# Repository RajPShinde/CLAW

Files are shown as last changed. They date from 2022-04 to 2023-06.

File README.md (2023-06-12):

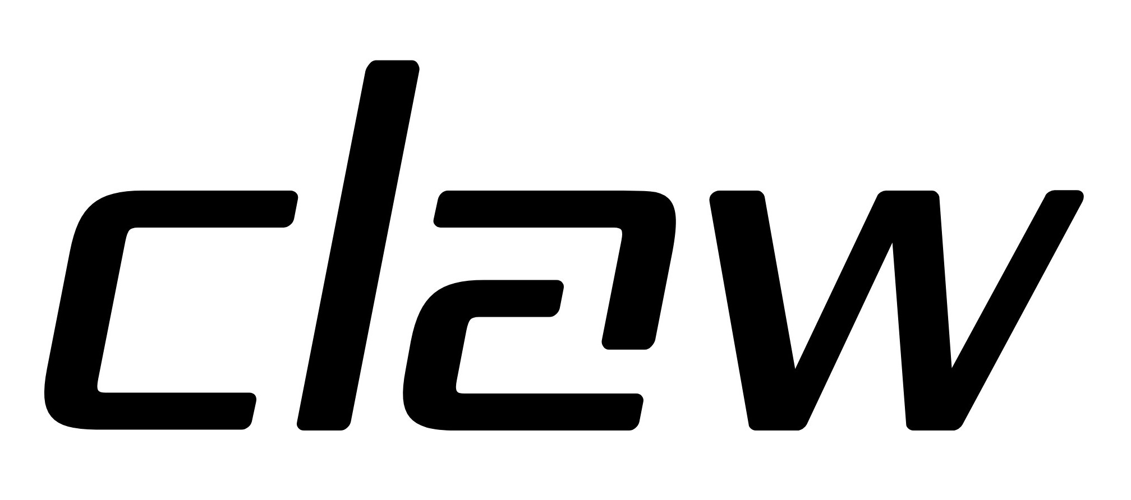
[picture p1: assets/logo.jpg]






---

## Overview
<p align="center">

</p>
An Open Source Quadruped Robot.
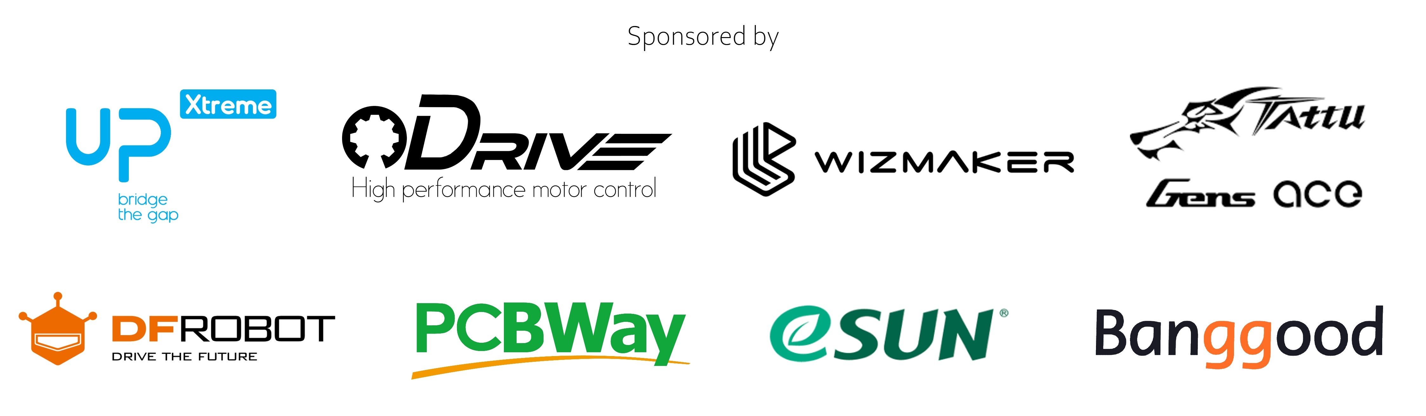
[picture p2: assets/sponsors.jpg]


## Dependencies
1. [ROS Noetic](http://wiki.ros.org/noetic)
2. [OCS2](https://github.com/leggedrobotics/ocs2)
3. [Eigen 3.4.0](https://eigen.tuxfamily.org/index.php?title=Main_Page)
4. [odrive_can](https://github.com/swankun/odrive_can)
5. [U8g2](https://github.com/olikraus/u8g2)

## Hardware
1. UP Xtreme i12- Core i5-1250PE 16GB RAM
2. Odrive 3.6 Motor Controller
3. Intel Realsense D435i
4. 8308 90Kv Outrunner BLDC
5. AS5047P Encoder
6. MCP2515 CAN Controller
7. MPU9265 9-DOF IMU
8. ADS1115 4-Channel ADC
9. WS2812B Addressable LED
10. SHI1106 128X64 OLED
11. MD30-60 Pressure Sensor

## Install & Build
```
mkdir -p ~/claw_ws/src
cd ~/claw_ws/src
git clone https://github.com/RajPShinde/CLAW
```

## TO-DO's
### CAD
- [x] Parts
- [x] Assembly
- [x] URDF
### Hardware Interface
- [x] PCB Design
- [x] SPI Test
- [x] I2C Test (MPU9255 & SH1106)
- [x] Socket CAN Test (MCP2515)
### Kinematics
- [x] Inverse Kinematics
- [x] Forward Kinematics
- [x] Velocity Kinematics
### Controls
- [ ] Hybrid Control (Impedance + Position)
### Trajectory Planning
- [x] Compound Cycloid
- [x] Bezier Curve
- [x] Jerk Minimized
### Visualization
- [x] Joint State Publishers
### Manager
- [ ] State Machine

## LICENSE
```
BSD 3-Clause License

Copyright (c) 2023, Raj Shinde
All rights reserved.

Redistribution and use in source and binary forms, with or without
modification, are permitted provided that the following conditions are met:

1. Redistributions of source code must retain the above copyright notice, this
   list of conditions and the following disclaimer.

2. Redistributions in binary form must reproduce the above copyright notice,
   this list of conditions and the following disclaimer in the documentation
   and/or other materials provided with the distribution.

3. Neither the name of the copyright holder nor the names of its
   contributors may be used to endorse or promote products derived from
   this software without specific prior written permission.

THIS SOFTWARE IS PROVIDED BY THE COPYRIGHT HOLDERS AND CONTRIBUTORS "AS IS"
AND ANY EXPRESS OR IMPLIED WARRANTIES, INCLUDING, BUT NOT LIMITED TO, THE
IMPLIED WARRANTIES OF MERCHANTABILITY AND FITNESS FOR A PARTICULAR PURPOSE ARE
DISCLAIMED. IN NO EVENT SHALL THE COPYRIGHT HOLDER OR CONTRIBUTORS BE LIABLE
FOR ANY DIRECT, INDIRECT, INCIDENTAL, SPECIAL, EXEMPLARY, OR CONSEQUENTIAL
DAMAGES (INCLUDING, BUT NOT LIMITED TO, PROCUREMENT OF SUBSTITUTE GOODS OR
SERVICES; LOSS OF USE, DATA, OR PROFITS; OR BUSINESS INTERRUPTION) HOWEVER
CAUSED AND ON ANY THEORY OF LIABILITY, WHETHER IN CONTRACT, STRICT LIABILITY,
OR TORT (INCLUDING NEGLIGENCE OR OTHERWISE) ARISING IN ANY WAY OUT OF THE USE
OF THIS SOFTWARE, EVEN IF ADVISED OF THE POSSIBILITY OF SUCH DAMAGE.
```

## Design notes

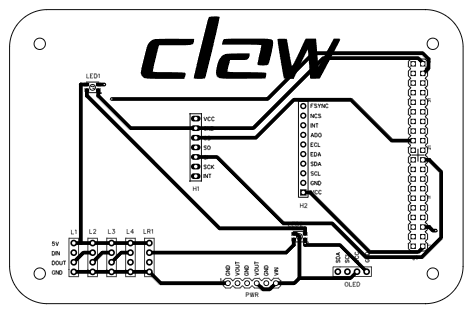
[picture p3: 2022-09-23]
PCB/PCB.png

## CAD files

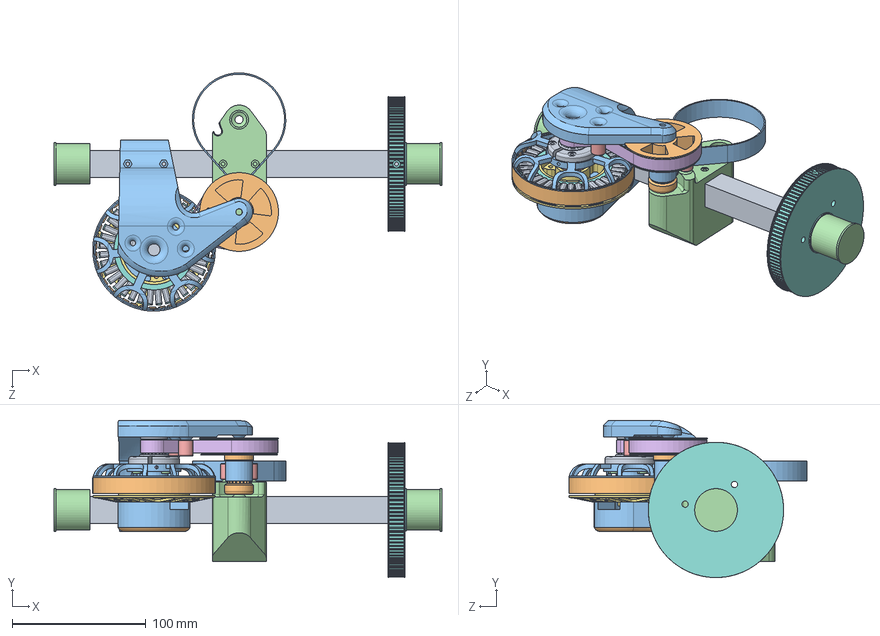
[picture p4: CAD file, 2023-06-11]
CAD/Assembly/Front Right Hip.SLDASM
290.3 x 117.6 x 178.3 mm
Hip Flexion & Abduction- HTD 3M 20T
Hip Flexion- HTD 3M 20T-60T
Hip Flexion- Motor Holder (Mirror)
Leg Holder (Mirror)
3xMR115 x 4
HTD 3M 10mm x 276mm
base.stp
stator.stp
coil.stp x 36
rotor.stp
outrunner.stp
screw-mount.stp x 4
6702ZZ-bearing-15x21x4.stp x 2
shaft.stp
fix-screw.stp
Hip Abduction- HTD 3M 105T (Mirror)
CF Hip
Hip Flexion Motor Holder Cover (Mirror)
HTD3M 15mm x 300mm
Shoulder Axle x 2

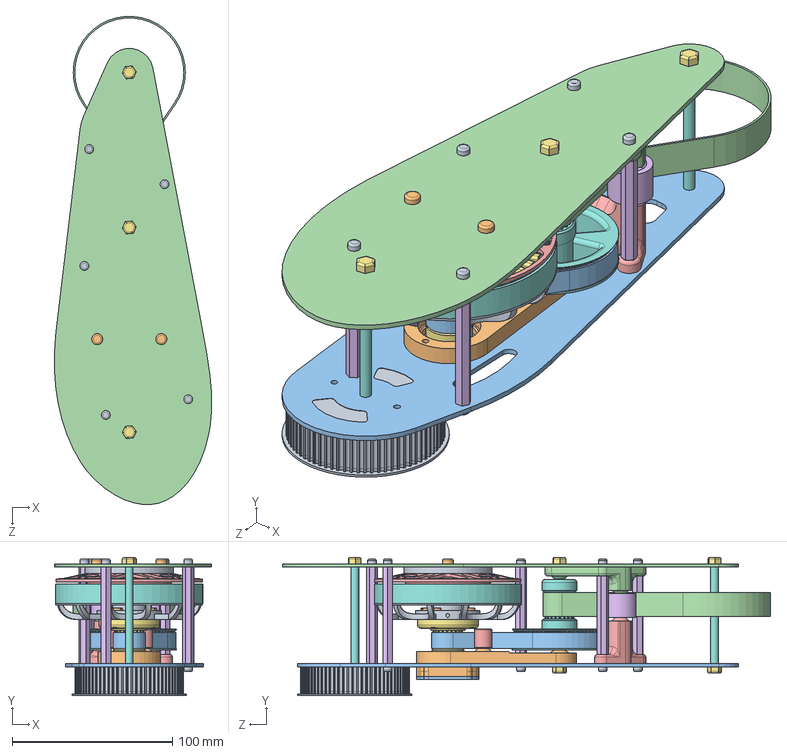
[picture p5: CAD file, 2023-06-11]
CAD/Assembly/Left Thigh.SLDASM
98.2 x 86.3 x 304.5 mm
Knee Motor Spacer
Knee Tensioner 1
Leg Plate- Inner
Leg Plate- Outer
base.stp
stator.stp
coil.stp x 36
rotor.stp
outrunner.stp
screw-mount.stp x 4
6702ZZ-bearing-15x21x4.stp x 2
shaft.stp
fix-screw.stp
Standoff 60mm x 5
Knee Flexion- HTD 3M 20T
Knee Flexion- HTD 3M 20T-60T
Hip Flexion- HTD 3M 72T
Knee Encoder Bottom Holder
Knee Encoder Top Holder
Knee Tensioner 2 Outer (Left Leg)
Knee Tensioner 2 Inner (Left Leg)
Knee Flexion- Idler x 2
M5 Nut x 5
M5 60mm x 2
M3 Screw 10mm x 10
M5 Screw 10mm x 2
HTD 3M 10mm x 276mm
HTD 3M 15mm x 348mm
3xMR115 x 2

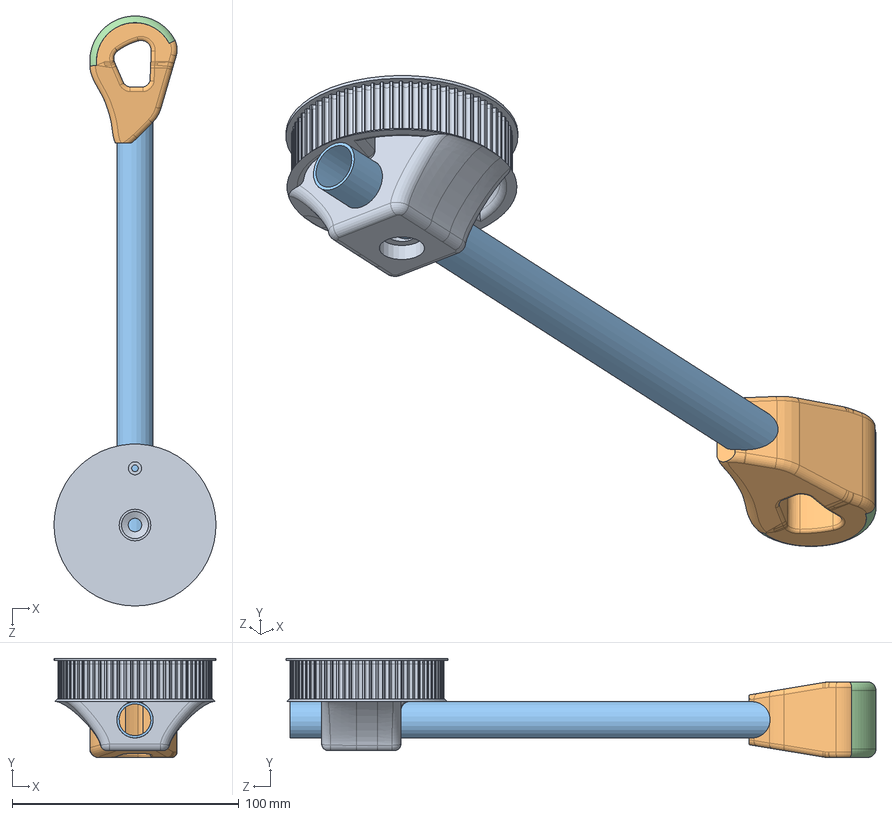
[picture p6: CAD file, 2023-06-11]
CAD/Assembly/Left Calf.SLDASM
71.4 x 43.8 x 260.2 mm
Knee Flexion- HTD 3M 72T
claw
CF Calf
Rubber Sole

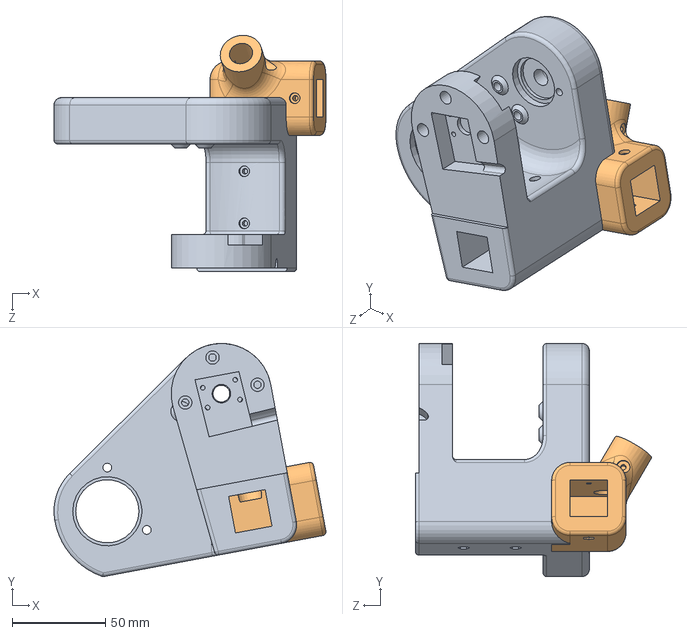
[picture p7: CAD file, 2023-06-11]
CAD/SPLDRT/Hip Abduction Motor Holder + Front Left Bracket.SLDASM
146.2 x 125.3 x 127.1 mm
Motor Holder- Hip Abduction
Front Left L Bracket

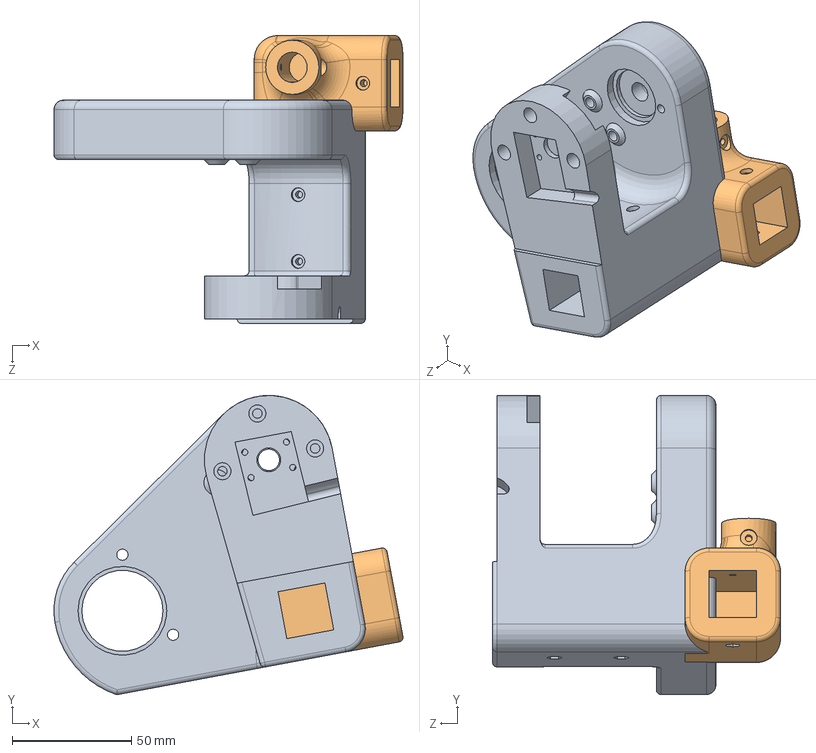
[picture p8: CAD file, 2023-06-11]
CAD/SPLDRT/Hip Abduction Motor Holder + Rear Right Bracket.SLDASM
146.2 x 125.3 x 120.7 mm
Motor Holder- Hip Abduction
Rear Right L Bracket

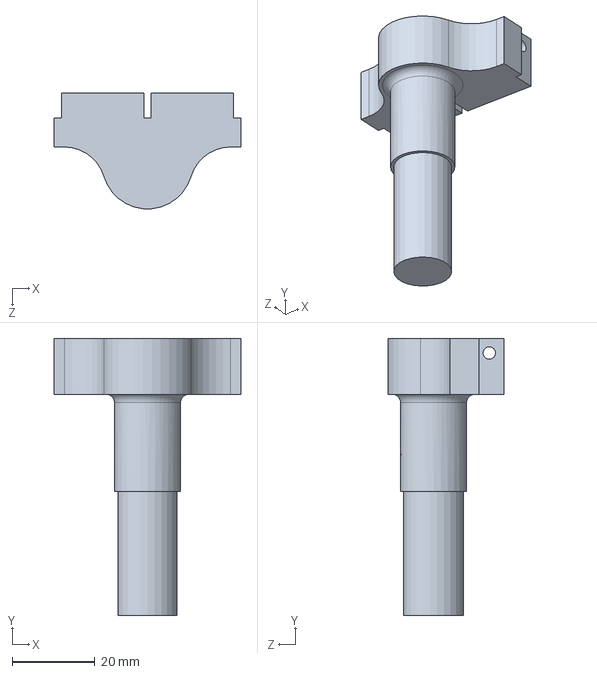
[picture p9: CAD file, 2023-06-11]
CAD/SPLDRT/Front Odrive Bracket.SLDPRT
45.1 x 67.0 x 27.9 mm

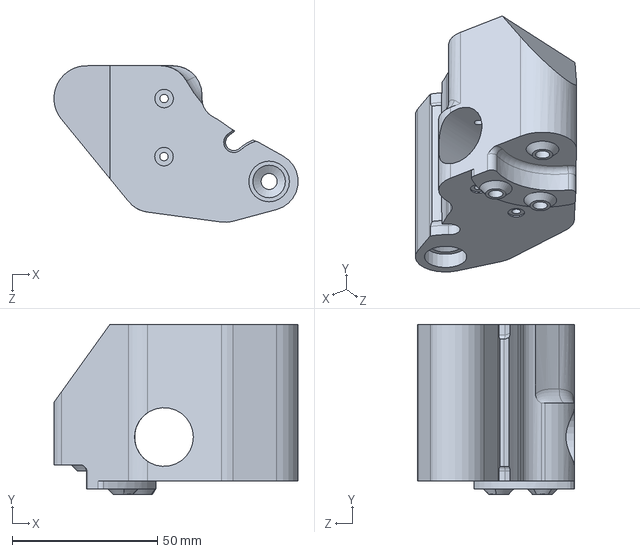
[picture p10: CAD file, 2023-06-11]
CAD/SPLDRT/Leg Hip Holder- Left.SLDPRT
84.0 x 58.6 x 53.9 mm

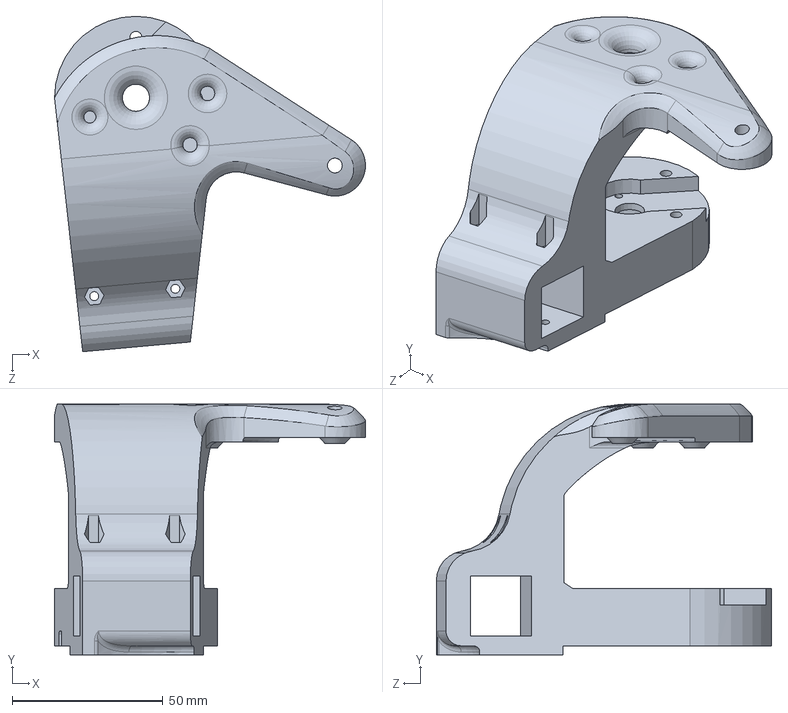
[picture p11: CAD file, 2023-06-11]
CAD/SPLDRT/Hip Flexion- Motor Holder.SLDPRT
103.1 x 83.1 x 111.2 mm

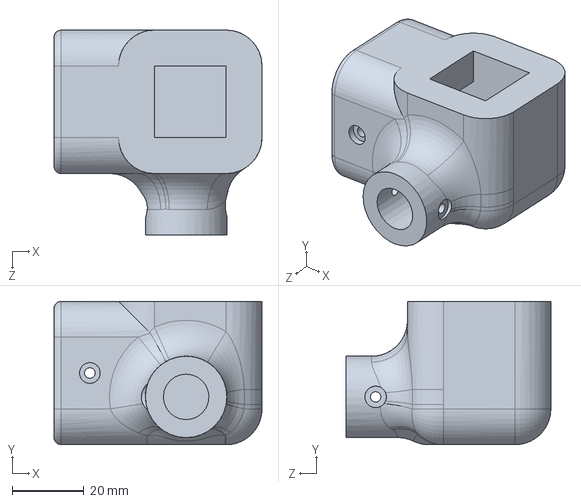
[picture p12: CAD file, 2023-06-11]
CAD/SPLDRT/Rear Right L Bracket.SLDPRT
58.0 x 40.0 x 57.1 mm

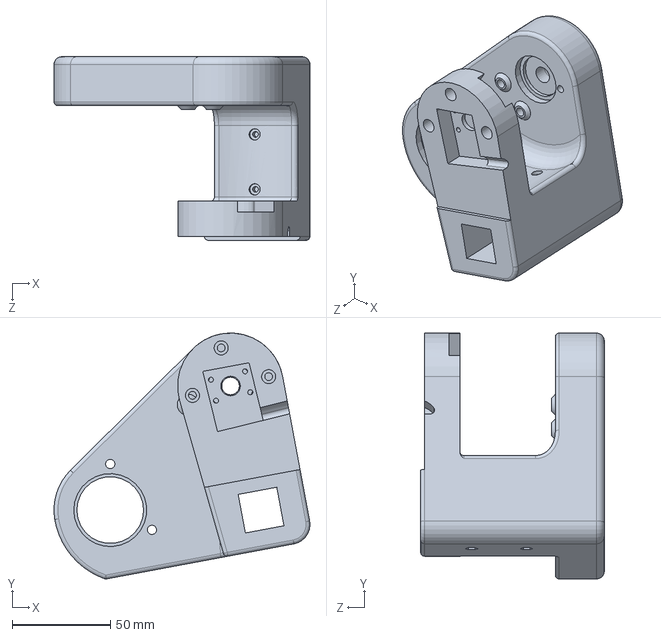
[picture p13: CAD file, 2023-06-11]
CAD/SPLDRT/Motor Holder- Hip Abduction.SLDPRT
130.5 x 125.3 x 93.6 mm

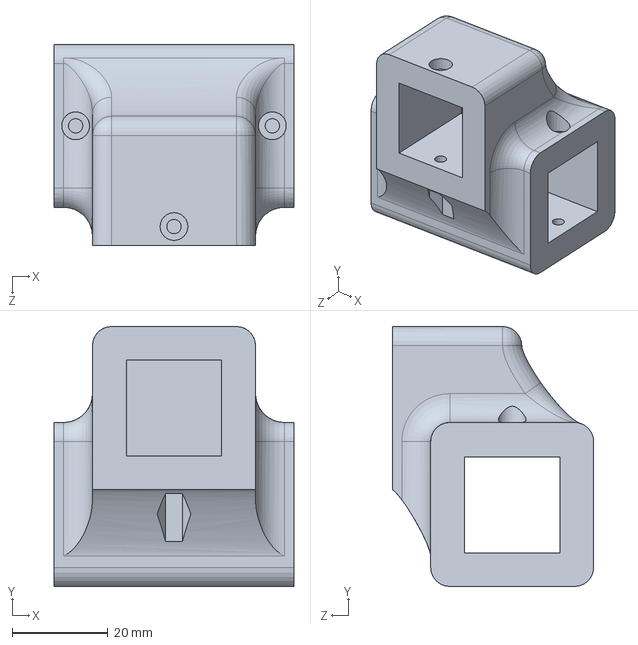
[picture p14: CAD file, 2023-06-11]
CAD/SPLDRT/Deck Holder.SLDPRT
50.0 x 54.2 x 42.0 mm

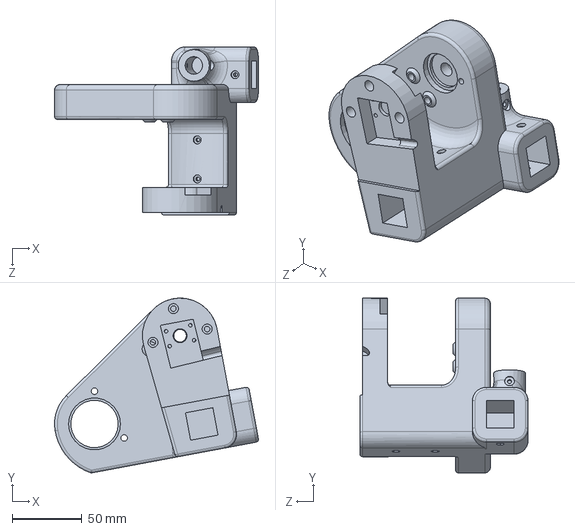
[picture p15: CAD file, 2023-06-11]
CAD/SPLDRT/Hip Abduction- Rear Right Motor Holder.SLDPRT
146.3 x 125.3 x 120.7 mm

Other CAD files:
CAD/Assembly/Rear Right Hip.SLDASM
CAD/Assembly/Right Thigh.SLDASM
CAD/Assembly/Front Left Hip.SLDASM
CAD/Assembly/Right Calf.SLDASM
CAD/Assembly/Rear Left Hip.SLDASM
CAD/SPLDRT/Motor Holder- Hip Abduction (Mirror).SLDPRT
CAD/Assembly/Off the shelf/Antenna/Antenna - Lambdoid - LWC-GSM-RD-RA-SMA-PLUG-02.SLDPRT
CAD/Assembly/Off the shelf/Antenna/Antenna - Lambdoid - LWC-GSM-RD-RA-SMA-PLUG-02.STEP
CAD/Assembly/Off the shelf/E-Stop/E-Stop.stp
CAD/Assembly/Off the shelf/Fan/40x40x10 fan cooler 5v sunon.SLDASM
CAD/Assembly/Off the shelf/Fan/40x40x10.SLDPRT
CAD/Assembly/Off the shelf/Fan/Cover.SLDPRT
CAD/Assembly/Off the shelf/Fan/Fan_Assembly.STEP
CAD/Assembly/Off the shelf/Fan/blade.SLDPRT
CAD/Assembly/Off the shelf/LA8308 90kv/motor-X83008S.stp
CAD/Assembly/Off the shelf/MPU9255/MIC5205 Low Noise LDO, MPU-9255.SLDPRT
CAD/Assembly/Off the shelf/MPU9255/MPU-9255 IC.SLDPRT
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

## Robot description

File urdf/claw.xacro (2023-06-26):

<?xml version="1.0"?>
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
<robot xmlns:xacro="http://www.ros.org/wiki/xacro" name="claw">
  <link name="base">
    <inertial>
      <origin xyz="0 0 0" rpy="0 0 0" />
      <mass value="6" />
      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
    </inertial>
    
    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

  </link>
  <link name="LF_hip">
    <inertial>
      <origin xyz="0.13174967055832 -0.00901971527534615 0.0213366444705591" rpy="0 0 0" />
      <mass value="1" />
      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
    </inertial>
    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

  </link>

  <joint name="LF_HAA" type="revolute">
    <origin xyz="0.0753395047601414 0.13942052488502 -0.0200209459409856" rpy="0 0 0" />
    <parent link="base" />
    <child link="LF_hip" />
    <axis xyz="1 0 0" />
    <dynamics damping="0" friction="0"/>
    <limit effort="35" velocity="21" lower="-0.35" upper="0.35"/>
  </joint>

  <link name="LF_thigh">
    <inertial>
      <origin xyz="0.00018271 0.010279 -0.079663" rpy="0 0 0" />
      <mass value="1.4" />
      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
    </inertial>
    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

  </link>

  <joint name="LF_HFE" type="revolute">
    <origin xyz="0.138495495239858 0 -0.0332000000000001" rpy="0 0 0" />
    <parent link="LF_hip" />
    <child link="LF_thigh" />
    <axis xyz="0 1 0" />
    <dynamics damping="0" friction="0"/>
    <limit effort="35" velocity="21" lower="-1.2" upper="1.2"/>
  </joint>

  <link name="LF_calf">
    <inertial>
      <origin xyz="-0.000287714806849276 0.0106638871413315 -0.0604997734780131" rpy="0 0 0" />
      <mass value="0.1" />
      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
    </inertial>
    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

  </link>

  <joint name="LF_KFE" type="revolute">
    <origin xyz="0 0 -0.22449657290337" rpy="0 0 0" />
    <parent link="LF_thigh" />
    <child link="LF_calf" />
    <axis xyz="0 1 0" />
    <dynamics damping="0" friction="0"/>
    <limit effort="35" velocity="21" lower="-2.45" upper="0"/>
  </joint>

  <link name="RF_hip">
    <inertial>
      <origin xyz="0.131752425088665 0.00909498645208687 0.0213386564682049" rpy="0 0 0" />
      <mass value="1" />
      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
    </inertial>
    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

  </link>

  <joint name="RF_HAA" type="revolute">
    <origin xyz="0.0753395047601412 -0.13952052488502 -0.0200212507695249" rpy="0 0 0" />
    <parent link="base" />
    <child link="RF_hip" />
    <axis xyz="1 0 0" />
    <dynamics damping="0" friction="0"/>
    <limit effort="35" velocity="21" lower="-0.35" upper="0.35"/>
  </joint>

  <link name="RF_thigh">
    <inertial>
      <origin xyz="-7.93319223516831E-05 -0.0101787998953494 -0.0796625362735511" rpy="0 0 0" />
      <mass value="1.4" />
      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
    </inertial>
    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

  </link>

  <joint name="RF_HFE" type="revolute">
    <origin xyz="0.138495495239859 0 -0.0331999999999995" rpy="0 0 0" />
    <parent link="RF_hip" />
    <child link="RF_thigh" />
    <axis xyz="0 1 0" />
    <dynamics damping="0" friction="0"/>
    <limit effort="35" velocity="21" lower="-1.2" upper="1.2"/>
  </joint>

  <link name="RF_calf">
    <inertial>
      <origin xyz="-0.000287481930574623 -0.0105530359423697 -0.0604998008854242" rpy="0 0 0" />
      <mass value="0.1" />
      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
    </inertial>
    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

  </link>

  <joint name="RF_KFE" type="revolute">
    <origin xyz="0 0 -0.22449657290337" rpy="0 0 0" />
    <parent link="RF_thigh" />
    <child link="RF_calf" />
    <axis xyz="0 1 0" />
    <dynamics damping="0" friction="0"/>
    <limit effort="35" velocity="21" lower="-2.45" upper="0"/>
  </joint>

  <link name="RH_hip">
    <inertial>
      <origin xyz="-0.131807126386722 0.00909513342303045 0.0213440413067441" rpy="0 0 0" />
      <mass value="1" />
      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
    </inertial>
    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

  </link>

  <joint name="RH_HAA" type="revolute">
    <origin xyz="-0.0753349999999998 -0.13952052488502 -0.0200212507695242" rpy="0 0 0" />
    <parent link="base" />
    <child link="RH_hip" />
    <axis xyz="1 0 0" />
    <dynamics damping="0" friction="0"/>
    <limit effort="35" velocity="21" lower="-0.35" upper="0.35"/>
  </joint>

  <link name="RH_thigh">
    <inertial>
      <origin xyz="-7.93319139673343E-05 -0.0101787999056125 -0.0796625362378313" rpy="0 0 0" />
      <mass value="1.4" />
      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
    </inertial>
    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

  </link>

  <joint name="RH_HFE" type="revolute">
    <origin xyz="-0.13883 0 -0.0332000000000001" rpy="0 0 0" />
    <parent link="RH_hip" />
    <child link="RH_thigh" />
    <axis xyz="0 1 0" />
    <dynamics damping="0" friction="0"/>
    <limit effort="35" velocity="21" lower="-1.2" upper="1.2"/>
  </joint>

  <link name="RH_calf">
    <inertial>
      <origin xyz="-0.000287472995257498 -0.0105530306508532 -0.0604997748556347" rpy="0 0 0" />
      <mass value="0.1" />
      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
    </inertial>
    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

  </link>

  <joint name="RH_KFE" type="revolute">
    <origin xyz="0 0 -0.22449657290337" rpy="0 0 0" />
    <parent link="RH_thigh" />
    <child link="RH_calf" />
    <axis xyz="0 1 0" />
    <dynamics damping="0" friction="0"/>
    <limit effort="35" velocity="21" lower="-2.45" upper="0"/>
  </joint>

  <link name="LH_hip">
    <inertial>
      <origin xyz="-0.131815401985864 -0.00901976754062939 0.0213456946368896" rpy="0 0 0" />
      <mass value="1" />
      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
    </inertial>
    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

  </link>

  <joint name="LH_HAA" type="revolute">
    <origin xyz="-0.0753349999999994 0.139420524885019 -0.0200209459409853" rpy="0 0 0" />
    <parent link="base" />
    <child link="LH_hip" />
    <axis xyz="1 0 0" />
    <dynamics damping="0" friction="0"/>
    <limit effort="35" velocity="21" lower="-0.35" upper="0.35"/>
  </joint>

  <link name="LH_thigh">
    <inertial>
      <origin xyz="0.000182705245315218 0.0102788070976663 -0.0796625722288096" rpy="0 0 0" />
      <mass value="1.4" />
      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
    </inertial>
    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

  </link>

  <joint name="LH_HFE" type="revolute">
    <origin xyz="-0.13883 0 -0.0332000000000001" rpy="0 0 0" />
    <parent link="LH_hip" />
    <child link="LH_thigh" />
    <axis xyz="0 1 0" />
    <dynamics damping="0" friction="0"/>
    <limit effort="35" velocity="21" lower="-1.2" upper="1.2"/>
  </joint>

  <link name="LH_calf">
    <inertial>
      <origin xyz="-0.000287712355231284 0.0106638796715953 -0.0604997404568841" rpy="0 0 0" />
      <mass value="0.1" />
      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
    </inertial>
    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

  </link>

  <joint name="LH_KFE" type="revolute">
    <origin xyz="0 0 -0.22449657290337" rpy="0 0 0" />
    <parent link="LH_thigh" />
    <child link="LH_calf" />
    <axis xyz="0 1 0" />
    <dynamics damping="0" friction="0"/>
    <limit effort="35" velocity="5" lower="-2.45" upper="0"/>
  </joint>

<joint name="LF_foot_fixed" type="fixed">
    <origin rpy="0 0 0" xyz="0 0 -0.2057"/>
    <parent link="LF_calf"/>
    <child link="LF_FOOT"/>
</joint>

<link name="LF_FOOT">
    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

    <inertial>
      <mass value="0.05"/>
      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
    </inertial>
</link>

<joint name="RF_foot_fixed" type="fixed">
    <origin rpy="0 0 0" xyz="0 0 -0.2057"/>
    <parent link="RF_calf"/>
    <child link="RF_FOOT"/>
</joint>

<link name="RF_FOOT">
    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

    <inertial>
      <mass value="0.05"/>
      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
    </inertial>
</link>

<joint name="RH_foot_fixed" type="fixed">
    <origin rpy="0 0 0" xyz="0 0 -0.2057"/>
    <parent link="RH_calf"/>
    <child link="RH_FOOT"/>
</joint>

<link name="RH_FOOT">
    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

    <inertial>
      <mass value="0.05"/>
      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
    </inertial>
</link>

<joint name="LH_foot_fixed" type="fixed">
    <origin rpy="0 0 0" xyz="0 0 -0.2057"/>
    <parent link="LH_calf"/>
    <child link="LH_FOOT"/>
</joint>

<link name="LH_FOOT">
    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

    <inertial>
      <mass value="0.05"/>
      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
    </inertial>
</link>

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
<joint name="imu_joint" type="fixed">
    <origin xyz="0 0 0" rpy="0 0 0"/>
    <parent link="base"/>
    <child link="imu"/>
</joint>
<link name="imu">
    <inertial>
        <mass value="0.01"/>
        <origin rpy="0 0 0" xyz="0 0 0"/>
        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
    </inertial>
    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
</link>

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

</robot>

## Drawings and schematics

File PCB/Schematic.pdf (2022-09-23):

A | A

1

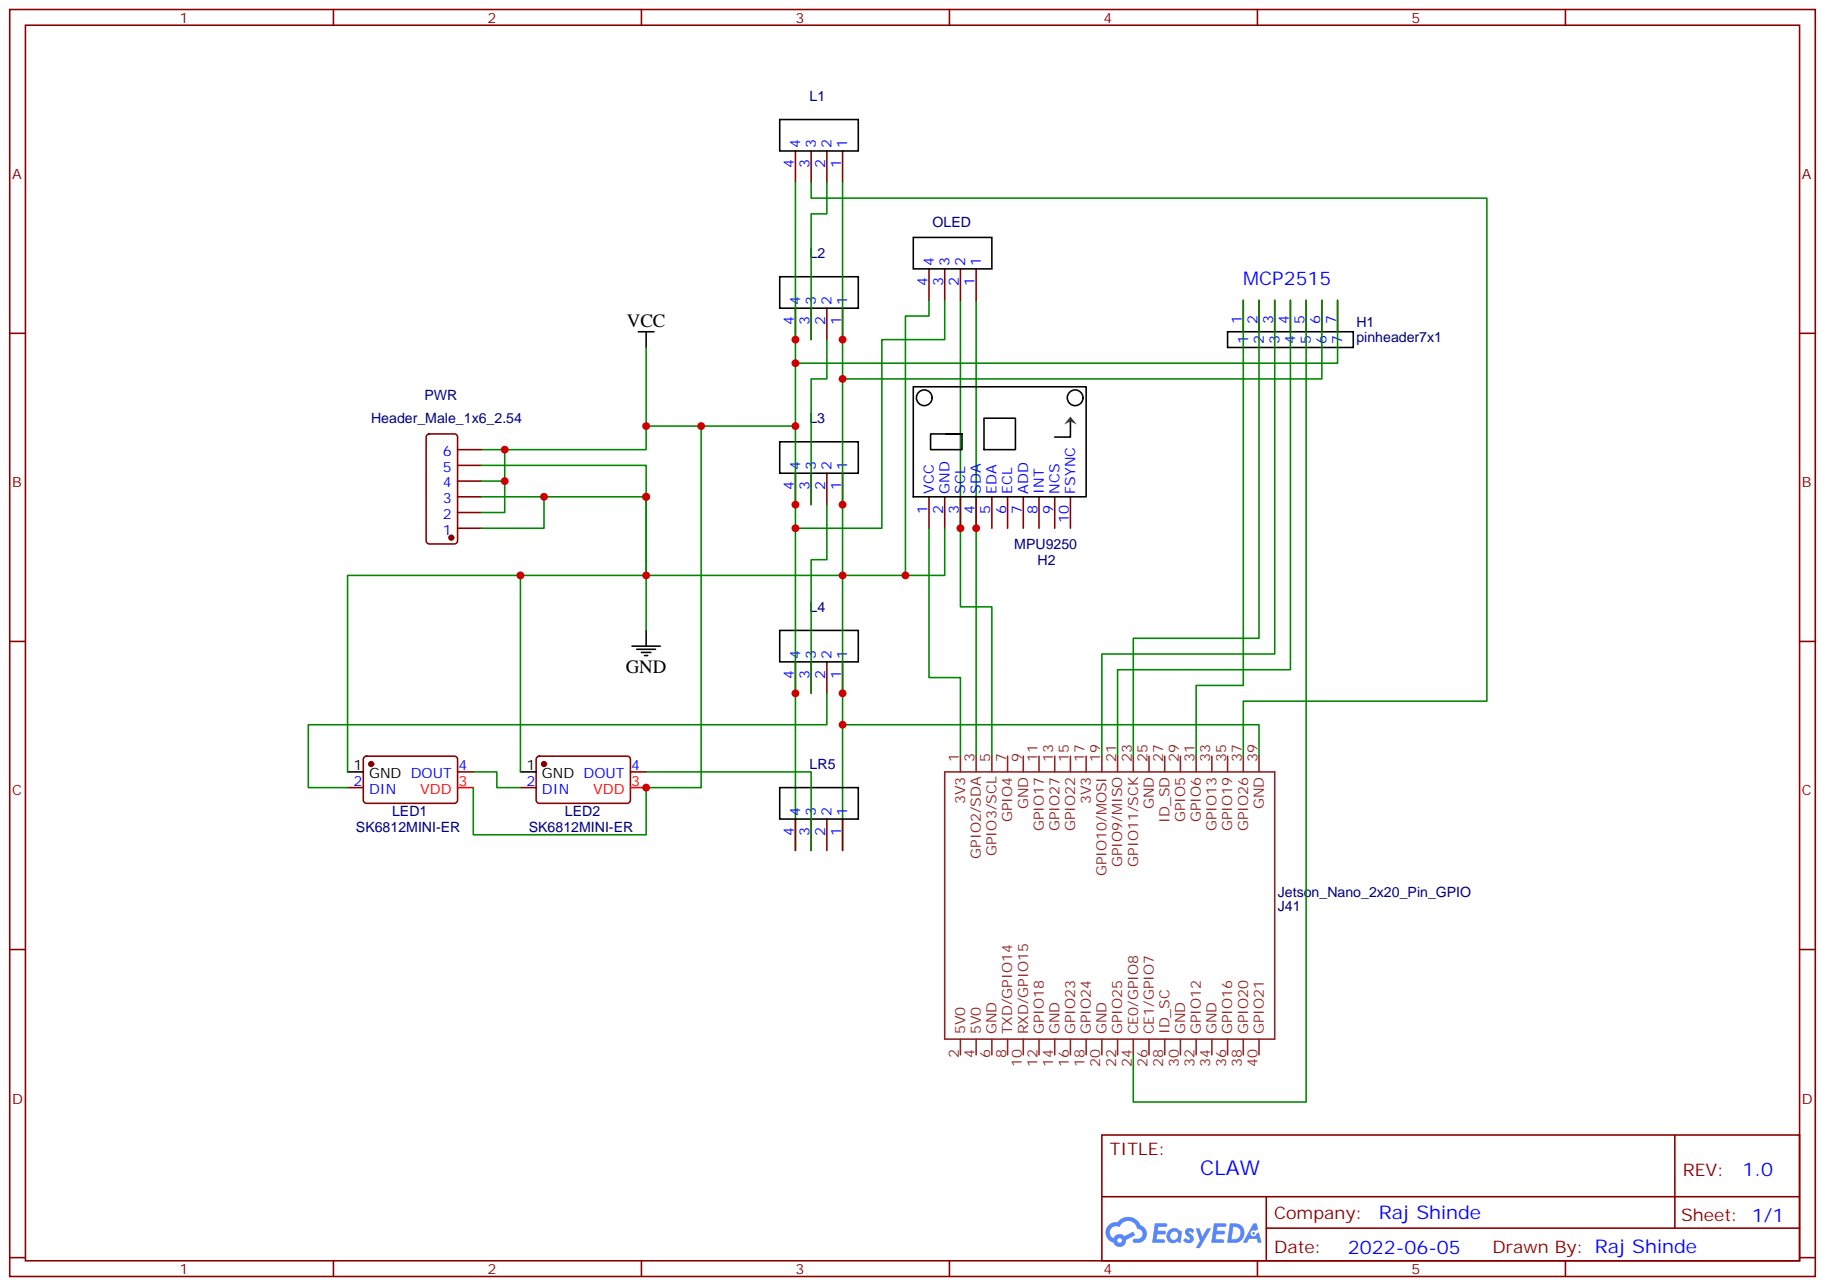
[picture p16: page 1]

GPIO21 40 GND 39 GPIO20 38 GPIO26 37 GPIO16 36 GPIO19 35 GND 34 GPIO13 33 GPIO12 32 GPIO6 31 GND 30 GPIO5 29 ID_SC 28 ID_SD 27 CE1/GPIO7 26 GND 25 CE0/GPIO8 24 GPIO11/SCK 23 GPIO25 22 GPIO9/MISO 21 GND 20 GPIO10/MOSI 19 GPIO24 18 3V3 17 GPIO23 16 GPIO22 15 GND 14 GPIO27 13 GPIO18 12 GPIO17 11 RXD/GPIO15 10 GND

Drawn By: Raj Shinde

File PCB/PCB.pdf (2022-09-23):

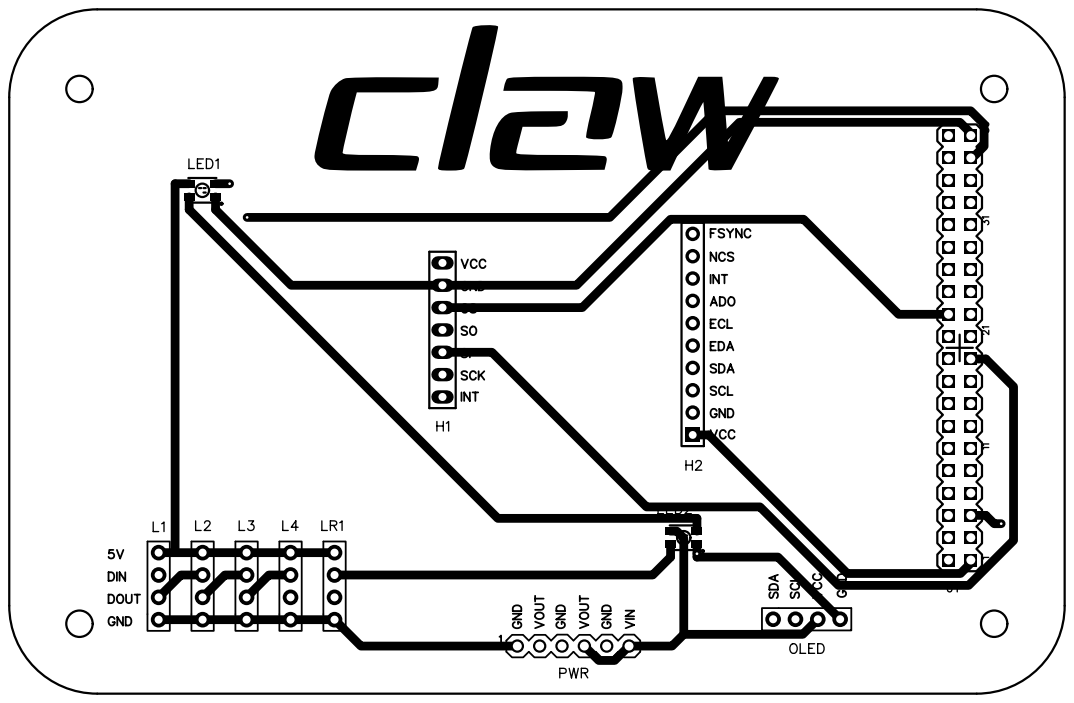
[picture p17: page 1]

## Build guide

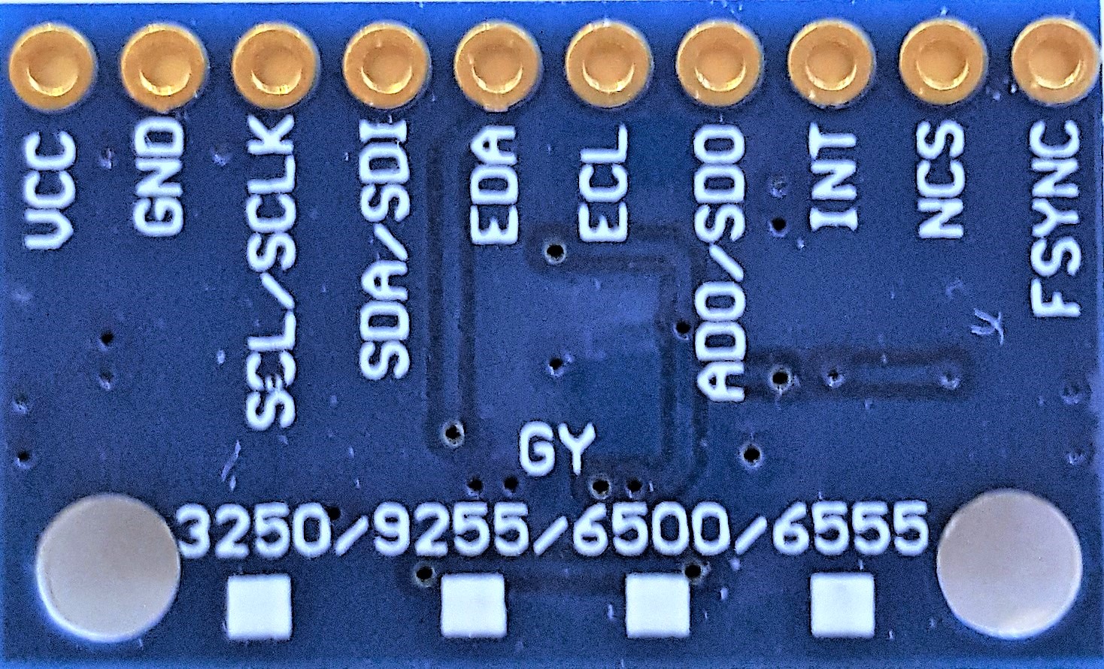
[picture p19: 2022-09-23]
CAD/Assembly/Off the shelf/MPU9255/Bottom View, MPU-9255.jpg

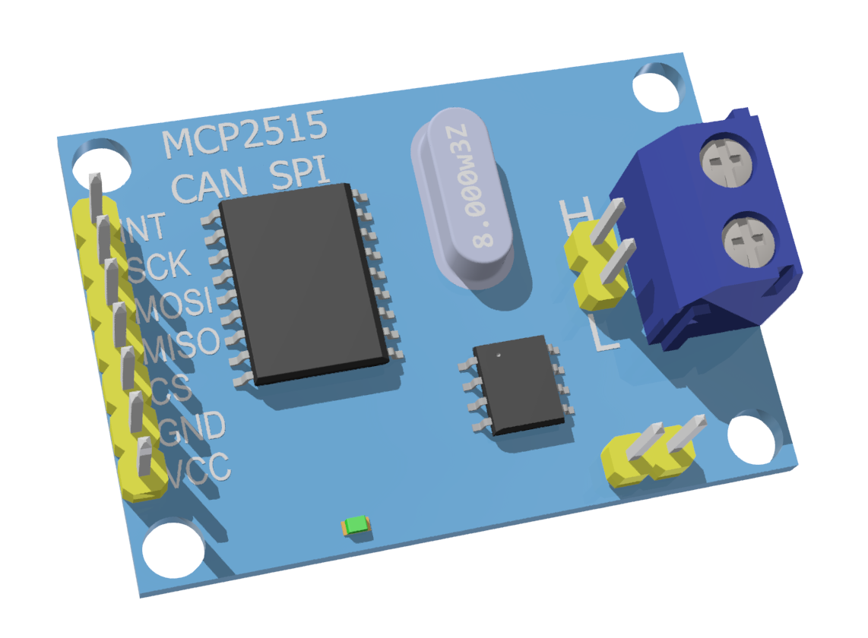
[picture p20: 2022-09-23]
CAD/Assembly/Off the shelf/MCP2515/MCP2515 CAN_SPI.PNG

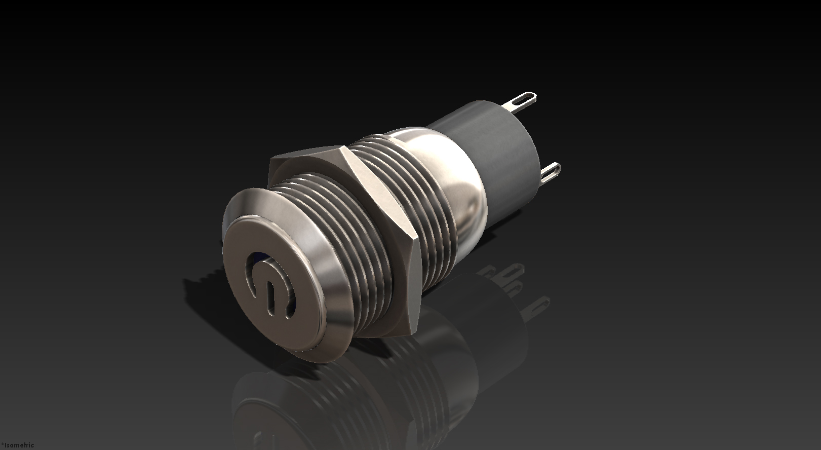
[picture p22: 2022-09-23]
CAD/Assembly/Off the shelf/Momentaty Push Button/PowerSwitch1.jpg

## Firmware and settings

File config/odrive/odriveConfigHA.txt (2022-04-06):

odrv0.axis0.motor.config.pole_pairs=20
odrv0.axis0.encoder.config.cpr = 2000
odrv0.axis0.motor.config.torque_constant=0.091888889
odrv0.config.dc_max_negative_current=-0.09
odrv0.axis0.controller.config.vel_limit=10
odrv0.axis0.requested_state = AXIS_STATE_FULL_CALIBRATION_SEQUENCE
odrv0.axis0.motor.config.pre_calibrated =True
odrv0.axis0.encoder.config.pre_calibrated =True
odrv0.axis0.requested_state = AXIS_STATE_ENCODER_INDEX_SEARCH
odrv0.axis0.config.startup_encoder_index_search = True
odrv0.axis0.config.startup_encoder_offset_calibration = False
odrv0.axis0.config.startup_closed_loop_control = True
odrv0.save_configuration()

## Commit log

2022-03-30 Add source & header for manager and kinematics
2022-04-01 Add stubs for kinematics & trajectory planning
2022-04-05 Add submodule for odrive_can and stubs for traj & kinematics
2022-04-06 Add methods for jerk minimized and cycloidal trajectories & odrive HA config
    [odriveConfigHA.txt]
2022-04-08 Add implementation for inverse kinematics equations and fix to optimal leg traj
2022-04-08 Add actuator constants and z offset to robot config
2022-04-08 Add leg forward kinematics and full body kinematics methods
2022-04-09 Add stubs for velocity kinematics and updated README
2022-04-09 Add complete Jacobian matrix and method for end effector velocities calculation
2022-05-02 Add updated electronic & mechanical constants and joint variables to manager
2022-05-02 Add fixes to function args related to leg number and time
2022-05-02 Add thread for can data acquisition & basic gait flow
2022-05-07 Add methods to convert Joint angles to encoder positions, and change data container types
2022-05-07 Add ROS Logging messages and updating of joint angles in master thread
2022-05-27 Add CAD files for Leg Plates, Tensioners & Pulleys
    [Hip Flexion- HTD 3M 20T.SLDPRT, Hip Flexion- HTD 3M 72T.SLDPRT, Knee Flexion- HTD 3M 20T-60T.SLDPRT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]
2022-06-24 Add CAD files for internal Leg Parts & gantry
    [40x40x10 fan cooler 5v sunon.SLDASM, 40x40x10.SLDPRT, Control Plate.SLDPRT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]
2022-06-25 Add fix to thread capture list and update main loop
2022-06-25 Add initializer list to gait.cpp & fix data containers in claw.hpp
    [claw.hpp]
2022-06-25 Add VelocityKinematics as a derived class of ForwardKinematics
2022-06-25 Update method names and fix variable referencing
    [main.cpp]
2022-06-25 Update CMakeLists to include eigen3 & socket_interfaces
2022-06-27 Update config dir structure for rviz and add a test launch file
    [odriveConfigHA.txt]
2022-06-27 Add new CAD for computer deck, tensioners and Body parts
    [Camera Holder.SLDPRT, Computer Deck.SLDPRT, Computer Holder.SLDPRT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]
2022-09-18 Add updated source for kinematics with new structs
2022-09-18 Add new and updated CAD's
    [20mm Tube Cover.SLDPRT, Battery Base.SLDPRT, Control Plate.SLDPRT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]
2022-09-18 Add python scripts to test hardware interface and to configure Odrives
2022-09-18 Add Leg Assembly and STL's for parts
    [20mm Tube Cover.STL, Battery Base.STL, Control Plate.STL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]
2022-09-18 Add MCP251X device tree overlay
2022-09-18 Add c++17 compile options & fix array initializer list size
    [claw.hpp]
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2022-09-19 Update odrive configuration with calibration_current & max_regen_current parameters
2022-09-19 Update sensorData thread to get encoder shadow counts
2022-09-23 Add CAD's for legs and hips
    [20mm Tube Cover.SLDPRT, 2xMR115.SLDPRT, 3xMR115.SLDPRT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]
2022-09-23 Add final robot assembly and updated leg assemblies
    [40x40x10 fan cooler 5v sunon.SLDASM, 40x40x10.SLDPRT, AZ-Delivery - OLED13 IIC.stp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]
2022-09-23 Add URDF & robot meshes for simulation and visulaization
    [claw.csv, claw.urdf, hip1.STL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]
2022-09-23 Add Schematics, PCB Design & Fabrication files
2022-10-08 Add joint state publisher & update launch files
2022-10-08 Add bezier based leg trajectory generation
2022-10-08 Fix robot TF's & add a dummy frame (not in URDF)
    [claw.hpp]
2022-10-09 Add method to transform trajectory to leg frame
2022-10-09 Add can parameter to robot constants & fix operator= for Point
    [claw.hpp]
2022-10-16 Add methods for odrive Initialization and gait generation loop
2022-10-17 Add method to IDLE all odrives
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2022-10-21 Update odrive configuration with brake resistor and regen current limit
2022-10-21 Add timer for status LED & change reative path to boot video
2022-10-21 Update status LED call to run in a different thread & update encoder directions for HF & KF
2022-10-21 Update method to compute odrive commands from IK output
2022-10-26 Add position gain and change CAN Bus bitrate for Odrives
2022-10-26 Add & update method to command Odrives and convert joint angles to counts
2022-10-26 Update script to set up CAN Bus & update encoder directions in robot constants
2022-12-24 Add updated launch files & odrive configuration script
2023-06-10 [CAD] Add updated interations of parts & remove depricated parts
    [Aluminum 750mm.SLDPRT, Aluminum 770mm.SLDPRT, CF 120mm.SLDPRT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]
2023-06-10 [CAD] Add updated Assemblies
    [Front Left Hip.SLDASM, Front Right Hip.SLDASM, Left Calf.SLDASM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]
2023-06-10 [CAD] Add STL's for 3D-Printable parts
    [Cover Rear 2.STL, Cover Rear.STL, Deck Holder.STL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]
2023-06-11 [boot] Update CAN driver dts with new Oscillator Frequency
2023-06-11 [scripts] Add installation script; Update scripts for foot LED's and sh1106 display
2023-06-26 [CAD] Remove depricated STL files
    [20mm Tube Cover.STL, Battery Base.STL, Control Plate.STL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]
2023-06-26 [hardwareInterface] Add odrive initialization and sensorInterface for IMU; Add containers for IMU and Actuator Data; Add constants for device ports and addresses
2023-06-26 [meshes] Add updated meshes for URDF
    [hip1.STL, hip2.STL, hip3.STL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]
2023-06-26 [urdf] Add updated URDF
    [claw.csv, claw.urdf, claw.xacro]
2023-07-03 [launch][scripts] Add updated launch files; Add script for URDF Generation
2023-07-03 Add methods to setup joints and handle for contactSensors; Add implementation for hybridJointHandle
2023-07-03 Update CMakeLists with compiler tags; Add kinematics as shared library; Add source file for hardwareInterface target
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2023-07-14 [contactSensor] Add read for sensor in a different thread
2023-10-27 [launch] Update launch files for interface and MPU9250 Driver
2023-10-27 [scripts] Add MPU9250 Driver and updated Odrive parameter
